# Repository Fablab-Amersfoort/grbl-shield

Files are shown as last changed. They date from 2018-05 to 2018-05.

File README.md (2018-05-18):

Grbl shield
-----------
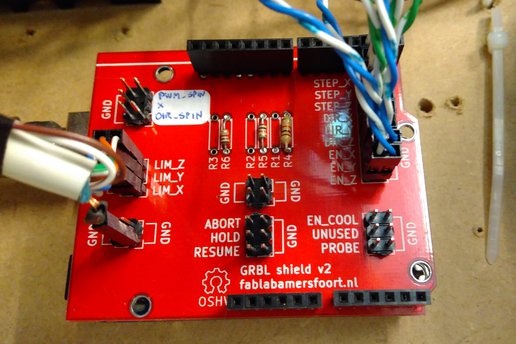
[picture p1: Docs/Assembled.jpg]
Assembled v2 board


This repository contains the KiCad design files for a grbl shield. It is
intended to for an Arduino Uno running [grbl][1], to connect it to
external stepper drivers, limit switches and other equipment. The reason
for developing this shield, instead of using an existing shield, is that
this shield has filtering applied to the limit pins to allow more robust
operation in a noisy environment (at [Fablab Amersfoort][2], our limit
switches were picking up noise from the parallely running spindle power
wires). Other than that, this is a trivial PCB, that just connects pin
headers to the Arduino pins.

[1]: https://github.com/grbl/grbl/
[2]: http://www.fablabamersfoort.nl

The repository contains the KiCad design files for the board, under
"Releases" in github we also have pre-generated gerber files to use. We
have a few spare boards from our own order, which you can [order through
tindie][tindie].

[tindie]: https://www.tindie.com/products/12515/

Grbl pinout
-----------
This shield supports both the old (0.8) and new (0.9) Grbl pinout. The
difference is that the limit Z and spindle enable pins are swapped, and
the latter is repurposed to a spindle PWM pin. For the spindle,
switching layouts is a matter of use the right connector (`SPIN_EN` or
`SPIN_PWM`), but for the z limit pin, a solder jumper needs to be
soldered in either position (since there is also a filter attached).

Ground connections
------------------
The shield connects all three Arduino ground pins to the ground plane.
Ideally, you would use only one pin to prevent ground loops, but I
wasn't sure which one to use. The one above the digital pins is very
close to the limit pin connector and filter, but looking at the Arduino
Uno schematic, there is quite some distance and some vias between that
pins and the microcontroller. The other two ground pins have a better
connection to the microcontroller, but are further away from the limit
pins. For now, all of them are connected, if this causes problems, we
could try disconnecting some ground pins.

SMD capacitors
--------------
The shield uses SMD components for the filter capacitors, to minimize
the distance (and inductance) from the filtered pins and the capacitors.
To simplify the layout, the resistors use through-hole versions instead.

In the prototype, 22nF was used, but in the final design these were
replaced by 10nF because that was what was available.

Empty components
----------------
A number of components on the limit pins are left empty (NC) in the
schematic. Initial testing shows these shouldn't be needed, but if
further problems crop up, they could be used to improve the stability of
the design by adding smaller pullup resistors (Arduino Uno internal ones
are fairly big at 20k-50k), or adding a second filter capacitor of a
different size.

Single-sided layout
-------------------
The original layout was made for single-sided milling on a CNC mill, so
the design does not use any vias. The v1 board was produced like
this, v2 was slightly modified for 2-layer commercial production (but it
should be easy to make it single-sided again).

License
-------
This design is made available under the CERN Open Hardware License,
version 1.2 or above. See LICENSE.txt for the full text of the license.

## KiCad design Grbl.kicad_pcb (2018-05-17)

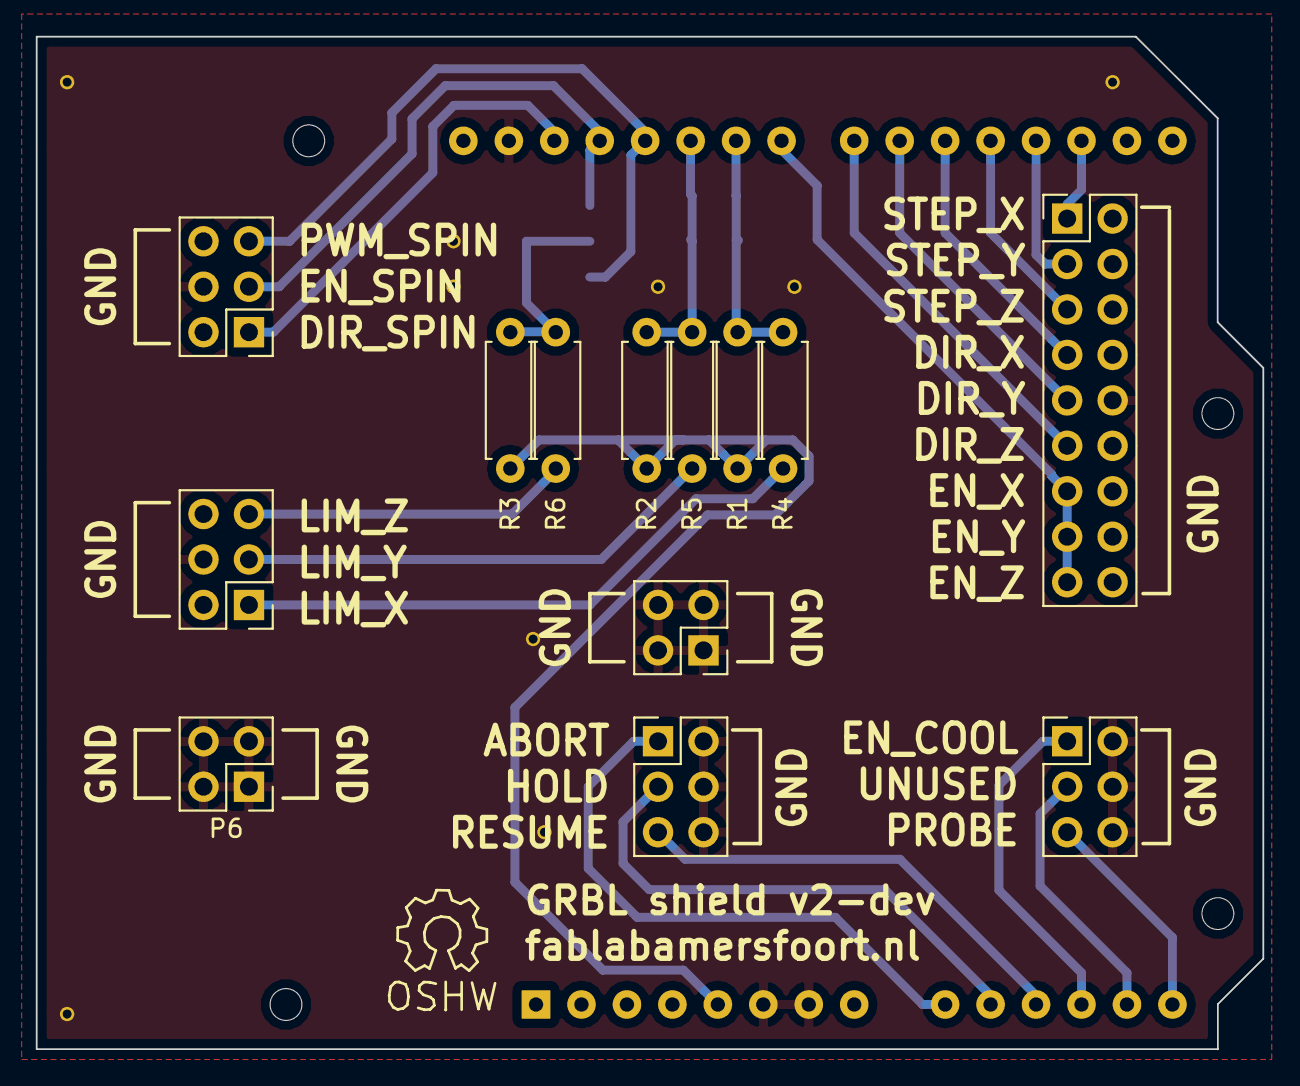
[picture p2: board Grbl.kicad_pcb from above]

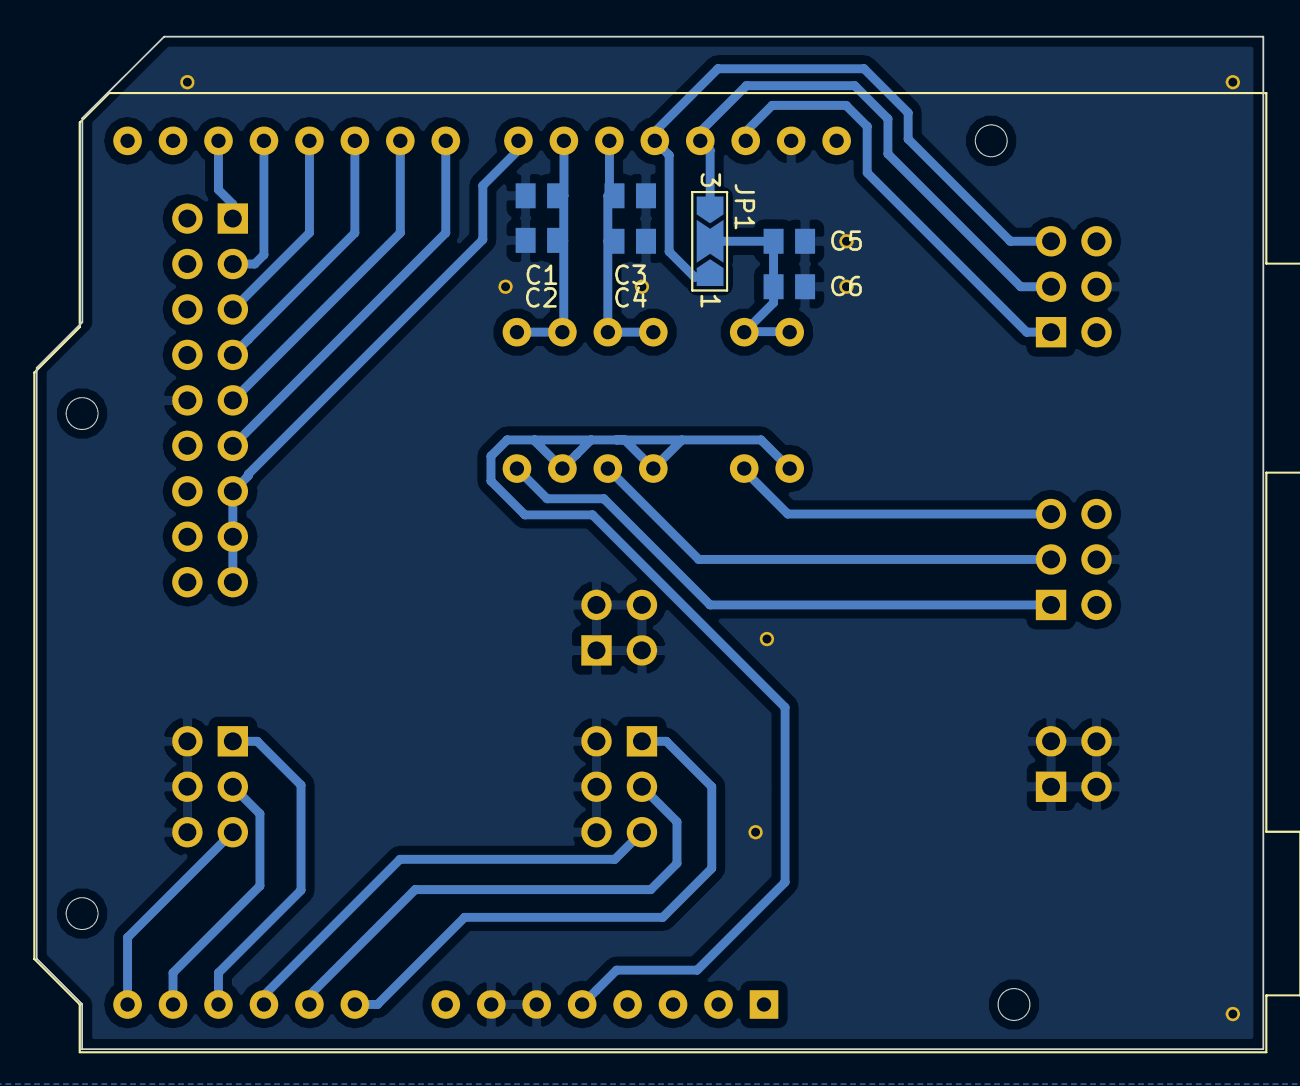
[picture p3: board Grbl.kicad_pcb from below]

Board: 2 copper layers, 68.5 x 56.6 mm, 21 parts (8 on the bottom side), 24 nets.

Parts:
C1, C3, C5: 10n; C_0805_2012Metric
C2, C4, C6: NC; C_0805_2012Metric
JP1: LAYOUT; SolderJumper-3_P2.0mm_Open_TrianglePad1.0x1.5mm_NumberLabels
P1: CTL; PinHeader_2x03_P2.54mm_Vertical
P2: MISC; PinHeader_2x03_P2.54mm_Vertical
P3: STEP; PinHeader_2x09_P2.54mm_Vertical
P4: SPIN; PinHeader_2x03_P2.54mm_Vertical
P5: LIMIT; PinHeader_2x03_P2.54mm_Vertical
P6, P7: GND; PinHeader_2x02_P2.54mm_Vertical
R1, R2, R3: NC; R_Axial_DIN0207_L6.3mm_D2.5mm_P7.62mm_Horizontal
R4, R5, R6: 1K; R_Axial_DIN0207_L6.3mm_D2.5mm_P7.62mm_Horizontal
SHIELD1: ARDUINO_UNO; Arduino_UNO_R2_WithMountingHoles

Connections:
+5V: R1.2, R2.2, R3.2, SHIELD1.5
/ABORT: P1.1, SHIELD1.9
/DIR_SPIN: P4.1, SHIELD1.28
/DIR_X: P3.7, SHIELD1.20
/DIR_Y: P3.9, SHIELD1.21
/DIR_Z: P3.11, SHIELD1.22
/EN_COOL: P2.1, SHIELD1.12
/EN_SPIN: JP1.3, P4.3, SHIELD1.27
/EN_X: P3.13, P3.15, P3.17, SHIELD1.23
/HOLD: P1.3, SHIELD1.10
/LIM_X: P5.1, R4.2
/LIM_X_FILTERED: C1.1, C2.1, R1.1, R4.1, SHIELD1.24
/LIM_Y: P5.3, R5.2
/LIM_Y_FILTERED: C3.1, C4.1, R2.1, R5.1, SHIELD1.25
/LIM_Z: P5.5, R6.2
/LIM_Z_FILTERED: C5.1, C6.1, JP1.2, R3.1, R6.1
/PROBE: P2.5, SHIELD1.14
/PWM_SPIN: JP1.1, P4.5, SHIELD1.26
/RESUME: P1.5, SHIELD1.11
/STEP_X: P3.1, SHIELD1.17
/STEP_Y: P3.3, SHIELD1.18
/STEP_Z: P3.5, SHIELD1.19
/UNUSED: P2.3, SHIELD1.13
GND: C1.2, C2.2, C3.2, C4.2, C5.2, C6.2, P1.2, P1.4, P1.6, P2.2, P2.4, P2.6, P3.10, P4.4, P5.4, P6.1, P6.2, P6.3, P6.4, P7.1, P7.2, P7.3, P7.4, SHIELD1.6, SHIELD1.7, SHIELD1.29

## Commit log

2015-12-21 Add first version of the KiCad design files
    [Grbl.kicad_pcb, Grbl.sch]
2017-07-06 Close the outline
    There was a tiny hole in the top right corner.
    [Grbl.kicad_pcb]
2017-07-06 Remove no longer existing library
    The Arduino symbol itself is still in the cache, but future designs
    should probably use the symbol shipped with KiCad instead.
    [Grbl.sch]
2017-07-06 Add more ground pins
    This helps connecting the shield wire of cables.
    [Grbl.kicad_pcb, Grbl.sch]
2017-07-06 Update silkscreen for two-layer version
    For the milled single layer version, there was copper on the back and
    "silkscreen" on the front. For a 2-layer version, there can be
    silkscreen on the back.
    This moves the refdes for capacitors to the back and removes the JP1
    label.
    [Grbl.kicad_pcb]
2017-07-06 Add a groundplane on the front
    This adds a filled zone and some vias.
    [Grbl.kicad_pcb]
2017-07-06 Add "GRBL shield v2" to the silkscreen
    [Grbl.kicad_pcb]
2017-07-06 Connect mounting holes to GND
    This changes the netname of the pads in the footprint, which won't
    survive a netleast re-read. There might be better approaches, but for
    now this works.
    [Grbl.kicad_pcb]
2017-07-06 Move some traces out of the way
    These were conflicting with the recently added GND header.
    [Grbl.kicad_pcb]
2017-07-07 Add board dimension markers
    These are just informative and will not show up on the board.
    [Grbl.kicad_pcb]
2017-07-07 Update plot options for Seeed
    [Grbl.kicad_pcb]
2017-07-18 Correct silkscreen for spindle pins
    These accidentially had the PWM_SPIN and DIR_SPIN labels swapped.
    [Grbl.kicad_pcb]
2018-05-17 Convert design to KiCad 5, with some changes
    This converts the design to use the newer KiCad 5 symbols and
    footprints, but additionally makes some changes:
    - The Arduino Uno symbol is now one from the default library instead of a
    third-party symbol, but it has a different pin numbering and layout.
    - The limit pin filtering schematic is a bit more spaced out, using net
    labels instead of direct connections.
    - The Arduino Uno footprint is now one from the default library and has
    two extra pins. It also has smaller mounting holes, see
    https://github.com/KiCad/kicad-footprints/issues/590
    - The solder jumper used was not available anymore, so a bigger one was
    used instead.
    [Grbl.kicad_pcb, Grbl.sch]
2018-05-17 README: Remove improvements
    The solder jumper was already made bigger, and making the traces bigger
    is only relevant when milling this manually, which I'll probably not be
    doing.
2018-05-17 README: Add image of assembled board
